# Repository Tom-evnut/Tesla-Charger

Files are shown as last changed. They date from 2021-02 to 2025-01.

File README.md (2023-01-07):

# Tesla-Charger
Reverse Engineering of the Tesla 10Kw charger and development of an open source control board.

PCB Files in DesignSpark 8 format.

Fully built and tested boards and bare PCBs available here :
http://www.evbmw.com/index.php/evbmw-webshop

Support forum : https://openinverter.org/forum/

19/10/17 : Uploaded two files : 
ph_frames.csv this file contains the 3 messages required to run phase module 1 in the Gen 2 charger
power_run_ph1.csv this is a capture of phase 1 starting up , ramping up to 8.5A DC 320VDC, 15.5A AC, 230v 50hz
Mains switched manually around message number 700 in ph_frames.csv

21/10/17 : Uploaded two files : 
power_run_ph1_arduino_2a_365vdc.csv
Tesla_chg1_1.ino
Crude arduino sketch to run one power module in the gen2 charger. Runs on an arduino due on CAN1

01/11/17 : Uploaded design files for Version 1 open source logic board for the Tesla Gen 2 charger. As of this date this design is totally unchecked and untested. Do not build this. It could blow up your house , car or cat. Based on the Arduino Due SAM3X8E microcontroller. Stay tuned.

05/11/17 : Updated Design files and PCBs ordered for prototype builds.

17/11/17 : BOM uploaded for the V1 board.

08/12/17 : Added Tesla_charger_Tom_v2_test.ino source file. Should run all 3 phases with the V1 logic board. Untested.

20/12/17 : Added design files for V2 Charger control board. Major changes :

Added 2M Serial EEPROM for parameter storage

Changed to a Vertical type B USB socket.

23/11/19 : Updated BOM for V4 with corrections.
27/02/18 : Error found on the V2 board. Missing grounds on Q1 and D5. Affects EVSE control only. Will ammend in a rev3 board asap.

28/02/18 : V3 design files released with grounds fixed. Also new S/W thanks to Tom DeBree released but untested as of today. Also pictures of mod required on V1 and V2 boards.

02/05/18 : V3 board and new software tested and working in my BMW E31 project car.

03/01/19 : Added an excellent user manual for the V3 logic board compiled by EVWest.

20/01/19 : Added a Beta Software directory to the Repo. Major changes as of this date :

-Stop sending power module can messages when charger not running - Working.

-Correct reading of charger Fault and Enable feedback signals - Working.

-Correct AC present flag so only sets if more than 70V AC is on each module - Working.

-Reset charger on detection of power module fault - Testing.

-Shutdown on exceeding a preset HV Battery voltage - Working. 

-Evse read routine now in 500ms loop to prevent false triggering -Working.

Recommend using this version.

27/01/19 : Added counter/timer to autoshutdown routine to prevent false triggering on transients.

06/02/19 : On request by a customer:

Added manual control mode for use of charger without EVSE. Digital one in when brought to +12v commands the charger to start
and when brought low commands charger off.

This mode also control HVDC via digital out 1 and AC mains via a contactor via Digital out 2.-Untested as of this date.

19/06/19 : Added schematic for V4 logic board design. V4 has the following upgrades over V3 :

-Changed from Type B USB to Mini. This will allow the charger lid to close without modification.

-Added extra stage of filtering to proximity signal.

-Single wire CAN capability added using the NCV7356. Now uses the exact same switching method between pwm control pilot and sw can as used in the Tesla charger / bms boards. This will allow use of Tesla destination charging, Chademo adapter,CCS adapter and possibly supercharging. All software dependent.

-Added two high power DC low side contactor drivers for use with DC fast charge or as general outputs.

-Added 3rd CAN channel based around the MCP2517 controller. Allows for high speed as well as FD Can. This extra can channel will allow the Tesla charger to act as a Chademo controller. Just add contactors and a hall current sensor.

-Two extra filtered and protected 12v digital inputs. General use or chademo control.

-One extra filtered and protected analog input. General use or hall current sensor for chademo control.

Untested as of this date.

Enjoy!

23/11/19 : Updated BOM for V4 with corrections.

21/01/2020 : New V5 design based on the STM32F103C8T6 now released. Note that as of today no firmware is developed. Anyone want to lend a hand?

18/02/20 : Beata firmware for the V5 board released. Untested as of this release due to hardware delay. Uses ST CUBEIDE.

14.03/20 : ESP8266 based web interface for the V5 charger board using Olimex module. Firmware uploaded. Untested as of release. Bench tests on V5 hardware looking good. One software bug discovered.

12/07/20 : 

Update : V5 software debugging now done.

-EEPROM saving of parameters now working.

-Autoshutdown on exceeding termination voltage parameter now working. 

-WiFi now working

-Correct reporting of voltage and current values over wifi and serial

-Robust reading of pilot pwm current setting. Was very noise prone.

Still todo : 

- Add support for the alternate CAN messaging in some chargers.

Release :

As stated previously due to the lack of engagement / support by the community I employed a developer to debug the firmware at some considerable financial cost and my own time in testing. As such the source for this and further updates will be available to Patrons on Patreon only as of now.
https://www.patreon.com/evbmw

This may change in the future. Binaries are freely available on Github and all boards bought from the EVBMW store will be shipped with this version.
https://github.com/damienmaguire/Tesla-Charger/tree/master/V5/Software/Binary

29/12/20 : Added pdf schematics, board layout and Gerbers for the V5 Block 2 boards (latest release).

24/02/21 : Added pdf schematics, board layout and Gerbers for the V5 Block 3 boards (latest release). Some design improvements to take advantage of the new Openinverter based firmware :

https://openinverter.org/wiki/GEN2

As of this time design files are availabe to Patrons on the "design files" level or greater on Patreon. An opensource release will occur in the future.

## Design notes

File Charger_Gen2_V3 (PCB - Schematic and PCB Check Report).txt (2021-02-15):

Schematic and PCB Check Report
------------------------------

Report Written:     Tuesday, December 18, 2018
Design Path:        C:\Users\tomde\Documents\GitHub\Tesla-Charger\Charger_Gen2_V3.pcb
Design Title:       
Created:            03-Oct-17 12:16:38 PM
Last Saved:         18-Dec-18 12:34:57 PM
Editing Time:       2199 min
Units:              mm (precision 2)

Checking integrity of Schematic "C:\Users\tomde\Documents\GitHub\Tesla-Charger\Charger_Gen2_V3.sch" with PCB "C:\Users\tomde\Documents\GitHub\Tesla-Charger\Charger_Gen2_V3.pcb"
================================================================================================================================================================================

The PCB and Schematic designs do not match.
To bring them into line, you will need to make the following changes to the PCB design:

Component 'C-USC0805' package 'C0805' in PCB is newer version than Schematic, use Update Component to correct this.
Component 'C-USC1206' package 'C1206' in PCB is newer version than Schematic, use Update Component to correct this.
Component 'WE-CBF_0805' package '0805' in PCB is newer version than Schematic, use Update Component to correct this.
Component 'LED0805' package 'CHIPLED_0805' in PCB is newer version than Schematic, use Update Component to correct this.
Component 'R-US_R0805' package 'R0805' in PCB is newer version than Schematic, use Update Component to correct this.
Component 'ATSAM3X/AAU' package 'LQFP144' in PCB is newer version than Schematic, use Update Component to correct this.
Component 'CRYSTAL-3.2-2.5' package 'CRYSTAL-3.2-2.5' in PCB is newer version than Schematic, use Update Component to correct this.
Component 'RESONATOR_EPSON_FC_145' package 'RESONATOR_EPSON_FC_145' in PCB is newer version than Schematic, use Update Component to correct this.
Component 'VARISTORCN0603' package 'CT/CN0603' in PCB is newer version than Schematic, use Update Component to correct this.

End Of Report.

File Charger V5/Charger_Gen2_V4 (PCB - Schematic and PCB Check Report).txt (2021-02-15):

Schematic and PCB Check Report
------------------------------

Report Written:     Monday, January 21, 2019
Design Path:        C:\Users\tomde\Documents\GitHub\Tesla-Charger\Charger V5\Charger_Gen2_V4.pcb
Design Title:       
Created:            03-Oct-17 12:16:38 PM
Last Saved:         21-Jan-19 5:06:33 PM
Editing Time:       2537 min
Units:              mm (precision 2)

Checking integrity of Schematic "C:\Users\tomde\Documents\GitHub\Tesla-Charger\Charger V5\Charger_Gen2_V4.sch" with PCB "C:\Users\tomde\Documents\GitHub\Tesla-Charger\Charger V5\Charger_Gen2_V4.pcb"
======================================================================================================================================================================================================

End Of Report.

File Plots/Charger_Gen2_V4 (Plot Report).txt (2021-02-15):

Plot Report
-----------

Report Written:     Tuesday, December 18, 2018
Design Path:        C:\Users\tomde\Documents\GitHub\Tesla-Charger\Charger_Gen2_V4.pcb
Design Title:       
Created:            03-Oct-17 12:16:38 PM
Last Saved:         18-Dec-18 12:57:42 PM
Editing Time:       2218 min
Units:              mm (precision 2)

Device Settings
===============

Gerber Settings
===============

    Leading zero suppression.
    G01 assumed throughout.
    Line termination <*> <CR> <LF>.
    3.5 format absolute inches.

    Format commands defined in Gerber file.
    Aperture table defined in Gerber file.
    Hardware arcs allowed.

Drill Settings
==============

    Excellon Format 1    Format 3.5 absolute in inches.
    Leading zero suppression.

Plots Output
============

    Plot Job: "C:\Users\tomde\Documents\GitHub\Tesla-Charger\Charger_Gen2_V3.mop"

Gerber Output
=============

C:\Users\tomde\Documents\GitHub\Tesla-Charger\Plots\Charger_Gen2_V4 - Top Copper.gbr

    Layers:
    --------------
    Top Copper

    D-Code Shape  (thou)
    ------------------------------------------------
    D16    Round 10.00
    D19    Round 8.00
    D88    Round 374.02
    D89    Square 76.77
    D90    Round 76.77
    D91    Round 60.00
    D92    Round 59.06
    D93    Round 62.99
    D94    Round 79.72
    D95    Round 43.31
    D96    Round 133.86
    D97    Round 40.00
    D98    Round 19.69
    D99    Round 78.74
    D100   Round 9.84
    D101   Round 39.37
    D102   Round 11.81
    D103   Round 5.91
    D114   Rectangle 29.53 X 129.92  Rotation 90
    D115   Rectangle 151.57 X 196.85  Rotation 90
    D116   Rectangle 55.00 X 60.00
    D117   Rectangle 47.00 X 87.00
    D118   Rectangle 87.00 X 142.00  Rotation 90
    D119   Rectangle 42.13 X 85.04  Rotation 90
    D120   Rectangle 275.59 X 433.07
    D121   Rectangle 153.54 X 212.60
    D122   Rectangle 78.74 X 120.08  Rotation 90
    D123   Rectangle 49.21 X 157.48  Rotation 90
    D124   Rectangle 55.00 X 60.00  Rotation 90
    D125   Rectangle 62.99 X 133.86  Rotation 90
    D126   Square 63.00
    D127   Square 47.24
    D128   Rectangle 51.18 X 59.06
    D129   Rectangle 51.18 X 59.06  Rotation 90
    D130   Rectangle 11.81 X 47.24
    D131   Rectangle 11.81 X 47.24  Rotation 90
    D132   Rectangle 41.34 X 51.18
    D133   Rectangle 43.31 X 70.87
    D134   Square 39.37
    D135   Rectangle 30.00 X 95.00  Rotation 90
    D136   Rectangle 19.69 X 42.32  Rotation 90
    D137   Rectangle 19.69 X 42.32
    D138   Rectangle 27.56 X 39.37  Rotation 90
    D139   Rectangle 21.00 X 67.00  Rotation 90
    D140   Rectangle 27.56 X 60.04  Rotation 90
    D141   Rectangle 25.59 X 60.04  Rotation 90
    D142   Rectangle 25.00 X 50.00
    D143   Rectangle 118.11 X 141.73
    D144   Rectangle 102.36 X 118.11  Rotation 90

Gerber Output
=============

C:\Users\tomde\Documents\GitHub\Tesla-Charger\Plots\Charger_Gen2_V4 - Top Solder Mask.gbr

    Layers:
    -------------------
    Top Solder Mask

    D-Code Shape  (thou)
    ------------------------------------------------
    D118   Round 380.02
    D119   Rectangle 35.53 X 135.92  Rotation 90
    D120   Rectangle 157.57 X 202.85  Rotation 90
    D121   Square 82.77
    D122   Round 82.77
    D123   Rectangle 61.00 X 66.00
    D124   Rectangle 53.00 X 93.00
    D125   Rectangle 93.00 X 148.00  Rotation 90
    D126   Rectangle 48.13 X 91.04  Rotation 90
    D127   Rectangle 281.59 X 439.07
    D128   Rectangle 159.54 X 218.60
    D129   Rectangle 84.74 X 126.08  Rotation 90
    D130   Rectangle 55.21 X 163.48  Rotation 90
    D131   Rectangle 61.00 X 66.00  Rotation 90
    D132   Rectangle 68.99 X 139.86  Rotation 90
    D133   Round 66.00
    D134   Square 69.00
    D135   Square 53.24
    D136   Rectangle 57.18 X 65.06
    D137   Rectangle 57.18 X 65.06  Rotation 90
    D138   Rectangle 17.81 X 53.24
    D139   Rectangle 17.81 X 53.24  Rotation 90
    D140   Rectangle 47.34 X 57.18
    D141   Rectangle 49.31 X 76.87
    D142   Square 45.37
    D143   Rectangle 36.00 X 101.00  Rotation 90
    D144   Rectangle 25.69 X 48.32  Rotation 90
    D145   Rectangle 25.69 X 48.32
    D146   Rectangle 33.56 X 45.37  Rotation 90
    D147   Rectangle 27.00 X 73.00  Rotation 90
    D148   Rectangle 33.56 X 66.04  Rotation 90
    D149   Round 65.06
    D182   Round 68.99
    D183   Rectangle 31.59 X 66.04  Rotation 90
    D184   Round 85.72
    D185   Round 49.31
    D186   Round 139.86
    D187   Rectangle 31.00 X 56.00
    D188   Rectangle 124.11 X 147.73
    D189   Rectangle 108.36 X 124.11  Rotation 90
    D190   Round 46.00
    D191   Round 25.69
    D192   Round 84.74

Gerber Output
=============

C:\Users\tomde\Documents\GitHub\Tesla-Charger\Plots\Charger_Gen2_V4 - Top Paste Mask.gbr

    Layers:
    ------------------
    Top Paste Mask

    D-Code Shape  (thou)
    ------------------------------------------------
    D10    Rectangle 23.53 X 123.92  Rotation 90
    D11    Rectangle 145.57 X 190.85  Rotation 90
    D12    Rectangle 49.00 X 54.00
    D13    Rectangle 41.00 X 81.00
    D14    Rectangle 81.00 X 136.00  Rotation 90
    D15    Rectangle 36.13 X 79.04  Rotation 90
    D16    Rectangle 269.59 X 427.07
    D17    Rectangle 147.54 X 206.60
    D18    Rectangle 72.74 X 114.08  Rotation 90
    D19    Rectangle 43.21 X 151.48  Rotation 90
    D70    Rectangle 49.00 X 54.00  Rotation 90
    D71    Rectangle 56.99 X 127.86  Rotation 90
    D20    Square 57.00
    D21    Square 41.24
    D22    Rectangle 45.18 X 53.06
    D23    Rectangle 45.18 X 53.06  Rotation 90
    D24    Rectangle 5.81 X 41.24
    D25    Rectangle 5.81 X 41.24  Rotation 90
    D26    Rectangle 35.34 X 45.18
    D27    Rectangle 37.31 X 64.87
    D28    Square 33.37
    D29    Rectangle 24.00 X 89.00  Rotation 90
    D72    Rectangle 13.69 X 36.32  Rotation 90
    D73    Rectangle 13.69 X 36.32
    D74    Rectangle 21.56 X 33.37  Rotation 90
    D75    Rectangle 15.00 X 61.00  Rotation 90
    D76    Rectangle 21.56 X 54.04  Rotation 90
    D77    Rectangle 19.59 X 54.04  Rotation 90
    D78    Rectangle 19.00 X 44.00
    D79    Round 1.00
    D80    Rectangle 112.11 X 135.73
    D81    Rectangle 96.36 X 112.11  Rotation 90

Gerber Output
=============

C:\Users\tomde\Documents\GitHub\Tesla-Charger\Plots\Charger_Gen2_V4 - Top Silkscreen.gbr

    Layers:
    ------------------
    Top Silkscreen

    D-Code Shape  (thou)
    -----------------------
    D79    Round 1.00
    D82    Round 5.00
    D83    Round 5.76
    D84    Round 3.20
    D85    Round 4.00
    D86    Round 7.87
    D87    Round 12.00
    D88    Round 10.00
    D89    Round 3.94
    D90    Round 27.56
    D91    Round 8.00
    D92    Round 3.00
    D93    Round 0.80
    D94    Round 6.00
    D95    Round 8.20
    D96    Round 0.00
    D97    Round 25.00
    D98    Round 1.28

Gerber Output
=============

C:\Users\tomde\Documents\GitHub\Tesla-Charger\Plots\Charger_Gen2_V4 - Documentation.gbr

    Layers:
    -----------------
    Documentation

    D-Code Shape  (thou)
    -----------------------
    D82    Round 5.00
    D87    Round 12.00
    D99    Round 1.97

Gerber Output
=============

C:\Users\tomde\Documents\GitHub\Tesla-Charger\Plots\Charger_Gen2_V4 - +5Vcc Plane (Powerplane).gbr

    Layers:
    -------------------------------------------------------------------------------------
    +5Vcc Plane  - Plane Isolation Gap 10.00 Thermal Connect Width 10.00 with 4 Spokes

    D-Code Shape  (thou)
    -----------------------------------------
    D100   Round 394.02
    D101   Square 96.77
    D102   Round 96.77
    D103   Round 80.00
    D104   Round 79.06
    D105   Round 82.99
    D106   Round 99.72
    D107   Round 63.31
    D108   Round 153.86
    D109   Round 40.00  Thermal Relief Pad
    D110   Round 19.69  Thermal Relief Pad
    D111   Round 60.00
    D112   Round 98.74
    D113   Round 39.69

Gerber Output
=============

C:\Users\tomde\Documents\GitHub\Tesla-Charger\Plots\Charger_Gen2_V4 - GND Plane (Powerplane).gbr

    Layers:
    -----------------------------------------------------------------------------------
    GND Plane  - Plane Isolation Gap 10.00 Thermal Connect Width 10.00 with 4 Spokes

    D-Code Shape  (thou)
    -----------------------------------------
    D100   Round 394.02
    D101   Square 96.77
    D102   Round 96.77
    D103   Round 80.00
    D104   Round 79.06
    D105   Round 82.99
    D106   Round 99.72
    D107   Round 76.77  Thermal Relief Pad
    D108   Round 60.00  Thermal Relief Pad
    D109   Round 59.06  Thermal Relief Pad
    D110   Round 62.99  Thermal Relief Pad
    D111   Round 79.72  Thermal Relief Pad
    D112   Round 63.31
    D113   Round 153.86
    D114   Round 60.00
    D115   Round 39.69
    D116   Round 40.00  Thermal Relief Pad
    D117   Round 78.74  Thermal Relief Pad
    D150   Round 19.69  Thermal Relief Pad

Gerber Output
=============

C:\Users\tomde\Documents\GitHub\Tesla-Charger\Plots\Charger_Gen2_V4 - Bottom Copper.gbr

    Layers:
    -----------------
    Bottom Copper

    D-Code Shape  (thou)
    -----------------------
    D10    Round 374.02
    D11    Square 76.77
    D12    Round 76.77
    D13    Round 60.00
    D14    Round 59.06
    D15    Round 62.99
    D16    Round 79.72
    D17    Round 43.31
    D18    Round 133.86
    D19    Round 40.00
    D70    Round 19.69
    D71    Round 78.74
    D20    Round 10.00
    D21    Round 9.84
    D22    Round 39.37
    D23    Round 11.81
    D24    Round 8.00
    D25    Round 5.91

Gerber Output
=============

C:\Users\tomde\Documents\GitHub\Tesla-Charger\Plots\Charger_Gen2_V4 - Bottom Copper (Resist).gbr

    Layers:
    -----------------
    Bottom Copper

    D-Code Shape  (thou)
    -----------------------
    D26    Round 384.02
    D27    Square 86.77
    D28    Round 86.77
    D29    Round 70.00
    D72    Round 69.06
    D73    Round 72.99
    D74    Round 89.72
    D75    Round 53.31
    D76    Round 143.86

Gerber Output
=============

C:\Users\tomde\Documents\GitHub\Tesla-Charger\Plots\Charger_Gen2_V4 - Bottom Copper (Paste).gbr

    Layers:
    -----------------
    Bottom Copper

    D-Code Shape  (thou)
    -----------------------

NC Drill Output
===============

C:\Users\tomde\Documents\GitHub\Tesla-Charger\Plots\Charger_Gen2_V4 - Drill Data - [Through Hole].drl

    Output:
    -----------------------------
    Plated Round Drill Holes
    Unplated Round Drill Holes
    Plated Slots
    Unplated Slots
    Plated Board Outlines
    Unplated Board Outlines

    Tool  Size           Count   ID  (Plated/Unplated)
    -----------------------------------------------------------
    T001  0.01181 inches 131   T
    T002  0.02400 inches 75    I
    T003  0.02500 inches 1
    T004  0.02756 inches 5     R
    T005  0.03200 inches 2     H
    T006  0.03543 inches 7     P
    T007  0.03937 inches 2     C
    T008  0.05118 inches 30    O
    T009  0.05315 inches 4     Q
    T010  0.09055 inches 2     S
    T011  0.17717 inches 6     N
    -----------------------------------------------------------
    Total                265
    -----------------------------------------------------------

Gerber Output
=============

C:\Users\tomde\Documents\GitHub\Tesla-Charger\Plots\Charger_Gen2_V4 - Drill Ident Drawing - [Through Hole].gbr

    Layers:
    ------------------
    [Through Hole]

Drill Ident Drawing
===================

    Drill Plated Size Shape ID
    -----------------------------------
    39    Y      100  Round C
    32    Y      100  Round H
    24    Y      100  Round I
    177   Y      100  Round N
    51    Y      100  Round O
    35    Y      100  Round P
    53    Y      100  Round Q
    28    Y      100  Round R
    91    Y      100  Round S
    12    Y      100  Round T

    D-Code Shape  (thou)
    -----------------------
    D77    Round 100.00
    D78    Round 5.00

Gerber Output
=============

C:\Users\tomde\Documents\GitHub\Tesla-Charger\Plots\Charger_Gen2_V4 - Outline.gbr

    Layers:
    ------------------
    Board Outlines

    D-Code Shape  (thou)
    -----------------------
    D79    Round 12.00

End Of Report.

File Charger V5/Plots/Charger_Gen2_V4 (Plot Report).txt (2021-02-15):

Plot Report
-----------

Report Written:     Thursday, January 24, 2019
Design Path:        C:\Users\tomde\Documents\GitHub\Tesla-Charger\Charger V5\Charger_Gen2_V4.pcb
Design Title:       
Created:            03-Oct-17 12:16:38 PM
Last Saved:         24-Jan-19 4:52:12 PM
Editing Time:       2613 min
Units:              mm (precision 2)

Device Settings
===============

Gerber Settings
===============

    Leading zero suppression.
    G01 assumed throughout.
    Line termination <*> <CR> <LF>.
    3.5 format absolute inches.

    Format commands defined in Gerber file.
    Aperture table defined in Gerber file.
    Hardware arcs allowed.

Drill Settings
==============

    Excellon Format 1    Format 3.5 absolute in inches.
    Leading zero suppression.

Plots Output
============

    Plot Job: "C:\Users\tomde\Documents\GitHub\Tesla-Charger\Charger V5\Charger_Gen2_V4.mop"

Gerber Output
=============

C:\Users\tomde\Documents\GitHub\Tesla-Charger\Charger V5\Plots\Charger_Gen2_V4 - Top Copper.gbr

    Layers:
    --------------
    Top Copper

    D-Code Shape  (thou)
    ------------------------------------------------
    D10    Round 374.02
    D11    Square 76.77
    D12    Round 76.77
    D13    Round 60.00
    D14    Round 59.06
    D15    Round 62.99
    D16    Round 79.72
    D17    Round 43.31
    D18    Round 133.86
    D19    Round 40.00
    D70    Round 19.69
    D71    Round 78.74
    D20    Round 10.00
    D21    Round 9.84
    D22    Round 39.37
    D23    Round 11.81
    D24    Round 8.00
    D25    Round 5.91
    D79    Rectangle 29.53 X 129.92  Rotation 90
    D80    Rectangle 151.57 X 196.85  Rotation 90
    D81    Rectangle 55.00 X 60.00
    D82    Rectangle 47.00 X 87.00
    D83    Rectangle 87.00 X 142.00  Rotation 90
    D84    Rectangle 42.13 X 85.04  Rotation 90
    D85    Rectangle 275.59 X 433.07
    D86    Rectangle 153.54 X 212.60
    D87    Rectangle 78.74 X 120.08  Rotation 90
    D88    Rectangle 49.21 X 157.48  Rotation 90
    D89    Rectangle 55.00 X 60.00  Rotation 90
    D90    Rectangle 62.99 X 133.86  Rotation 90
    D91    Square 63.00
    D92    Square 47.24
    D93    Rectangle 51.18 X 59.06
    D94    Rectangle 51.18 X 59.06  Rotation 90
    D95    Rectangle 11.81 X 47.24
    D96    Rectangle 11.81 X 47.24  Rotation 90
    D97    Rectangle 41.34 X 51.18
    D98    Rectangle 43.31 X 70.87
    D99    Square 39.37
    D100   Rectangle 30.00 X 95.00  Rotation 90
    D101   Rectangle 19.69 X 42.32  Rotation 90
    D102   Rectangle 19.69 X 42.32
    D103   Rectangle 27.56 X 39.37  Rotation 90
    D104   Rectangle 21.00 X 67.00  Rotation 90
    D105   Rectangle 27.56 X 60.04  Rotation 90
    D106   Rectangle 25.59 X 60.04  Rotation 90
    D120   Rectangle 25.00 X 50.00
    D121   Rectangle 118.11 X 141.73
    D122   Rectangle 102.36 X 118.11  Rotation 90

Gerber Output
=============

C:\Users\tomde\Documents\GitHub\Tesla-Charger\Charger V5\Plots\Charger_Gen2_V4 - Top Solder Mask.gbr

    Layers:
    -------------------
    Top Solder Mask

    D-Code Shape  (thou)
    ------------------------------------------------
    D123   Round 380.02
    D124   Rectangle 35.53 X 135.92  Rotation 90
    D125   Rectangle 157.57 X 202.85  Rotation 90
    D126   Square 82.77
    D127   Round 82.77
    D128   Rectangle 61.00 X 66.00
    D129   Rectangle 53.00 X 93.00
    D130   Rectangle 93.00 X 148.00  Rotation 90
    D131   Rectangle 48.13 X 91.04  Rotation 90
    D132   Rectangle 281.59 X 439.07
    D133   Rectangle 159.54 X 218.60
    D134   Rectangle 84.74 X 126.08  Rotation 90
    D135   Rectangle 55.21 X 163.48  Rotation 90
    D136   Rectangle 61.00 X 66.00  Rotation 90
    D137   Rectangle 68.99 X 139.86  Rotation 90
    D138   Round 66.00
    D139   Square 69.00
    D140   Square 53.24
    D141   Rectangle 57.18 X 65.06
    D142   Rectangle 57.18 X 65.06  Rotation 90
    D143   Rectangle 17.81 X 53.24
    D144   Rectangle 17.81 X 53.24  Rotation 90
    D145   Rectangle 47.34 X 57.18
    D146   Rectangle 49.31 X 76.87
    D147   Square 45.37
    D148   Rectangle 36.00 X 101.00  Rotation 90
    D149   Rectangle 25.69 X 48.32  Rotation 90
    D150   Rectangle 25.69 X 48.32
    D151   Rectangle 33.56 X 45.37  Rotation 90
    D152   Rectangle 27.00 X 73.00  Rotation 90
    D153   Rectangle 33.56 X 66.04  Rotation 90
    D154   Round 65.06
    D155   Round 68.99
    D156   Rectangle 31.59 X 66.04  Rotation 90
    D157   Round 85.72
    D158   Round 49.31
    D159   Round 139.86
    D160   Rectangle 31.00 X 56.00
    D161   Rectangle 124.11 X 147.73
    D162   Rectangle 108.36 X 124.11  Rotation 90
    D163   Round 46.00
    D164   Round 25.69
    D165   Round 84.74

Gerber Output
=============

C:\Users\tomde\Documents\GitHub\Tesla-Charger\Charger V5\Plots\Charger_Gen2_V4 - Top Paste Mask.gbr

    Layers:
    ------------------
    Top Paste Mask

    D-Code Shape  (thou)
    ------------------------------------------------
    D150   Rectangle 23.53 X 123.92  Rotation 90
    D151   Rectangle 145.57 X 190.85  Rotation 90
    D152   Rectangle 49.00 X 54.00
    D153   Rectangle 41.00 X 81.00
    D154   Rectangle 81.00 X 136.00  Rotation 90
    D155   Rectangle 36.13 X 79.04  Rotation 90
    D156   Rectangle 269.59 X 427.07
    D157   Rectangle 147.54 X 206.60
    D158   Rectangle 72.74 X 114.08  Rotation 90
    D159   Rectangle 43.21 X 151.48  Rotation 90
    D160   Rectangle 49.00 X 54.00  Rotation 90
    D161   Rectangle 56.99 X 127.86  Rotation 90
    D162   Square 57.00
    D163   Square 41.24
    D164   Rectangle 45.18 X 53.06
    D165   Rectangle 45.18 X 53.06  Rotation 90
    D166   Rectangle 5.81 X 41.24
    D167   Rectangle 5.81 X 41.24  Rotation 90
    D168   Rectangle 35.34 X 45.18
    D169   Rectangle 37.31 X 64.87
    D170   Square 33.37
    D171   Rectangle 24.00 X 89.00  Rotation 90
    D172   Rectangle 13.69 X 36.32  Rotation 90
    D173   Rectangle 13.69 X 36.32
    D174   Rectangle 21.56 X 33.37  Rotation 90
    D175   Rectangle 15.00 X 61.00  Rotation 90
    D176   Rectangle 21.56 X 54.04  Rotation 90
    D177   Rectangle 19.59 X 54.04  Rotation 90
    D178   Rectangle 19.00 X 44.00
    D179   Round 1.00
    D180   Rectangle 112.11 X 135.73
    D181   Rectangle 96.36 X 112.11  Rotation 90

Gerber Output
=============

C:\Users\tomde\Documents\GitHub\Tesla-Charger\Charger V5\Plots\Charger_Gen2_V4 - Top Silkscreen.gbr

    Layers:
    ------------------
    Top Silkscreen

    D-Code Shape  (thou)
    -----------------------
    D10    Round 5.00
    D11    Round 5.76
    D12    Round 3.20
    D13    Round 4.00
    D14    Round 7.87
    D15    Round 12.00
    D16    Round 10.00
    D17    Round 3.94
    D18    Round 27.56
    D19    Round 8.00
    D70    Round 3.00
    D71    Round 0.80
    D20    Round 6.00
    D21    Round 8.20
    D22    Round 0.00
    D23    Round 25.00
    D24    Round 1.28
    D179   Round 1.00

Gerber Output
=============

C:\Users\tomde\Documents\GitHub\Tesla-Charger\Charger V5\Plots\Charger_Gen2_V4 - Documentation.gbr

    Layers:
    -----------------
    Documentation

    D-Code Shape  (thou)
    -----------------------
    D10    Round 5.00
    D15    Round 12.00
    D25    Round 1.97

Gerber Output
=============

C:\Users\tomde\Documents\GitHub\Tesla-Charger\Charger V5\Plots\Charger_Gen2_V4 - +5Vcc Plane (Powerplane).gbr

    Layers:
    -------------------------------------------------------------------------------------
    +5Vcc Plane  - Plane Isolation Gap 10.00 Thermal Connect Width 10.00 with 4 Spokes

    D-Code Shape  (thou)
    -----------------------------------------
    D26    Round 394.02
    D27    Square 96.77
    D28    Round 96.77
    D29    Round 80.00
    D72    Round 79.06
    D73    Round 82.99
    D74    Round 99.72
    D75    Round 43.31  Thermal Relief Pad
    D76    Round 63.31
    D77    Round 153.86
    D78    Round 40.00  Thermal Relief Pad
    D79    Round 19.69  Thermal Relief Pad
    D80    Round 60.00
    D81    Round 98.74
    D82    Round 39.69

Gerber Output
=============

C:\Users\tomde\Documents\GitHub\Tesla-Charger\Charger V5\Plots\Charger_Gen2_V4 - GND Plane (Powerplane).gbr

    Layers:
    -----------------------------------------------------------------------------------
    GND Plane  - Plane Isolation Gap 10.00 Thermal Connect Width 10.00 with 4 Spokes

    D-Code Shape  (thou)
    -----------------------------------------
    D26    Round 394.02
    D27    Square 96.77
    D28    Round 96.77
    D29    Round 80.00
    D72    Round 79.06
    D73    Round 82.99
    D74    Round 99.72
    D75    Round 43.31  Thermal Relief Pad
    D76    Round 63.31
    D77    Round 153.86
    D78    Round 40.00  Thermal Relief Pad
    D79    Round 19.69  Thermal Relief Pad
    D80    Round 60.00
    D82    Round 39.69
    D83    Round 76.77  Thermal Relief Pad
    D84    Round 60.00  Thermal Relief Pad
    D85    Round 59.06  Thermal Relief Pad
    D86    Round 62.99  Thermal Relief Pad
    D87    Round 79.72  Thermal Relief Pad
    D88    Round 78.74  Thermal Relief Pad

Gerber Output
=============

C:\Users\tomde\Documents\GitHub\Tesla-Charger\Charger V5\Plots\Charger_Gen2_V4 - Bottom Copper.gbr

    Layers:
    -----------------
    Bottom Copper

    D-Code Shape  (thou)
    -----------------------
    D16    Round 10.00
    D19    Round 8.00
    D89    Round 374.02
    D90    Square 76.77
    D91    Round 76.77
    D92    Round 60.00
    D93    Round 59.06
    D94    Round 62.99
    D95    Round 79.72
    D96    Round 43.31
    D97    Round 133.86
    D98    Round 40.00
    D99    Round 19.69
    D100   Round 78.74
    D101   Round 9.84
    D102   Round 39.37
    D103   Round 11.81
    D104   Round 5.91

Gerber Output
=============

C:\Users\tomde\Documents\GitHub\Tesla-Charger\Charger V5\Plots\Charger_Gen2_V4 - Bottom Copper (Resist).gbr

    Layers:
    -----------------
    Bottom Copper

    D-Code Shape  (thou)
    -----------------------
    D105   Round 384.02
    D106   Square 86.77
    D107   Round 86.77
    D108   Round 70.00
    D109   Round 69.06
    D110   Round 72.99
    D111   Round 89.72
    D112   Round 53.31
    D113   Round 143.86

Gerber Output
=============

C:\Users\tomde\Documents\GitHub\Tesla-Charger\Charger V5\Plots\Charger_Gen2_V4 - Bottom Copper (Paste).gbr

    Layers:
    -----------------
    Bottom Copper

    D-Code Shape  (thou)
    -----------------------

NC Drill Output
===============

C:\Users\tomde\Documents\GitHub\Tesla-Charger\Charger V5\Plots\Charger_Gen2_V4 - Drill Data - [Through Hole].drl

    Output:
    -----------------------------
    Plated Round Drill Holes
    Unplated Round Drill Holes
    Plated Slots
    Unplated Slots
    Plated Board Outlines
    Unplated Board Outlines

    Tool  Size           Count   ID  (Plated/Unplated)
    -----------------------------------------------------------
    T001  0.01181 inches 131   T
    T002  0.02400 inches 75    I
    T003  0.02500 inches 1
    T004  0.02756 inches 5     R
    T005  0.03200 inches 2     H
    T006  0.03543 inches 7     P
    T007  0.03937 inches 2     C
    T008  0.05118 inches 30    O
    T009  0.05315 inches 4     Q
    T010  0.09055 inches 2     S
    T011  0.17717 inches 6     N
    -----------------------------------------------------------
    Total                265
    -----------------------------------------------------------

Gerber Output
=============

C:\Users\tomde\Documents\GitHub\Tesla-Charger\Charger V5\Plots\Charger_Gen2_V4 - Drill Ident Drawing - [Through Hole].gbr

    Layers:
    ------------------
    [Through Hole]

Drill Ident Drawing
===================

    Drill Plated Size Shape ID
    -----------------------------------
    39    Y      100  Round C
    32    Y      100  Round H
    24    Y      100  Round I
    177   Y      100  Round N
    51    Y      100  Round O
    35    Y      100  Round P
    53    Y      100  Round Q
    28    Y      100  Round R
    91    Y      100  Round S
    12    Y      100  Round T

    D-Code Shape  (thou)
    -----------------------
    D10    Round 5.00
    D114   Round 100.00

End Of Report.

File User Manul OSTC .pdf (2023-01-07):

## Serial Control Open Source Tesla Charger

By Tom de Bree 12/11/2018

## Contents

### Command Index

‘s’ to toggle the charge on and off by serial command, will be overridden in auto start and can control

‘d’ stops the debug and displays all the values currently set, will bring up display like below

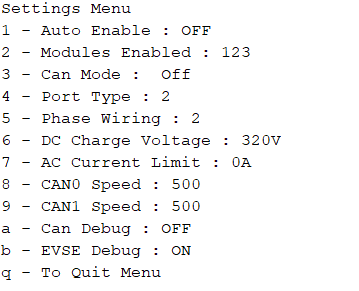
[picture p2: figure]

‘1’ to toggle auto enable, this looks at the pilot and proximity signal to turn the charger on and off.

‘2’ followed by which charger modules to enable; ‘12’ would enable module 1 and 2

‘3’ followed by a

‘0’ to disable can mode

‘1’ to enable can mode : Master

‘2’ to enable can mode : Master Elcon

‘3’ to enable can mode : Slave

‘4’ followed by a ‘1’ for a type 1 socket and ‘2’ for a type 2 socket.

‘5’ followed by a ‘1’ for single phase setup and ‘3’ for a three phase setup

‘6’ followed by the value for desired DC voltage in whole numbers in V

‘7’ followed by the value for desired AC current in whole numbers in A

‘8’ followed by a number to set canbus 1 speeds; ex: ‘8 250’ will give you a speed of 250 000 baud

‘9’ followed by a number to set canbus 1 speeds; ex: ‘9 250’ will give you a speed of 250 000 baud

‘a’ to toggle the Can Debug to be enabled once exiting the settings menu

‘b’ to toggle the EVSE Debug to be enabled once exiting the settings menu

## Recommended test settings

### Setup for using with EVSE

This setup is meant to be used when a charger is connected to a charging port and is meant to be used with an EVSE

- set it to can mode Master
- set it to autostart mode
- set 5 amp ac input limit per phase
- set end voltage limit suited to pack
- set to type 2 socket or set it to ‘t1’ for the type 1 socket
- Phase ‘3’ – if all modules are on their own phase, else use ‘1’

To initiate charge connect HV to charger and insert EVSE plug into socket.

If all works as expected change the input limit to match the wiring and breaker limits.

### Setup for using without EVSE

This setup is meant to be used when a charger is connected to a charging port and will not be used with an EVSE.

- set it to can master mode
- set it to No autostart mode
- set a 5 amp ac input limit per phase
- set end voltage limit suited to pack
- Phase ‘3’ – if all modules are on their own phase, else use ‘1’

To initiate charge connect HV to charger, command ‘s’ and apply AC power once module readouts appear on serial console.

If all works as expected change the input limit to match the wiring and breaker limits.

### Setup for configuring a Slave Charger

This setup is meant to be used when a charger is the second charger in a set. The other charger needs to be set to Can Mode: Master or Master Elcon.

- set it to can mode Slave
- set it to no autostart mode
- set a 5 amp ac input limit per phase
- set end voltage limit suited to pack
- Phase ‘3’ – if all modules are on their own phase, else use ‘1’

To initiate charge connect HV to charger and get the master charger to start charging (AC current limit for master charger needs to be above 15A). The slave charger will initiate shortly after the master.

If all works as expected change the input limit to match the wiring and breaker limits.

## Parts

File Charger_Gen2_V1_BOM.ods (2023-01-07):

Tesla Gen 2 Charger Logic Board V1
Ref Name | Qty | Component | Value | Manufacturer | MPN | RS Part Number | Mouser Part Number | Description
D3,4,5 | 3 | 1N4148WS-7-F |  | Diodes Inc. | 1N4148WS-7-F | 9228070 |  | Diode Switching 150mA 75V 200mW SOD323 Diodes Inc 1N4148WS-7-F Switching Diode, 150mA 75V, 2-Pin SOD-323
CONN3,4 | 2 | 3WAY_SIL |  | AMPHENOL FCI | 77311-401-36LF | 771-0189 |  | Board-To-Board Connector, 2.54 mm, 36 Contacts, Header, BergStik 77311 Series, Through Hole, 1 Rows
CONN2 | 1 | IPS1-115-01-S-D-PL |  | SAMTEC | IPS1-115-01-S-D-PL | 767-6859 |  | SAMTEC - IPS1-115-01-S-D-PL - SOCKET, 2.54MM, 2X15WAY
CONN1 | 1 | 24PinJSTCPT |  | JST (JAPAN SOLDERLESS TERMINALS) | SM24B-CPTK-1A-TB(L) |  | 306-SM24B-CPTK-1ATBL | Automotive Connectors 24 POS SIDE ENTRY CPT MALE CONN
L1 | 1 | 7447709470 |  | Wurth Elektronik | 7447709470 | 789-6805 |  | Surface Mount Power Inductor, WE-PD Series, 47 µH, 3.8 A, 4.5 A, Shielded, 0.06 ohm
IC1 | 1 | ATSAM3X/AAU | ATSAM3X8EA-AU | Microchip | ATSAM3X8EA-AU | 131-1191 | 556-ATSAM3X8EA-AU | ATSAM3X8EA-AU, 32bit ARM Cortex M3 Microcontroller, 84MHz, 512 kB Flash, 144-Pin LQFP
C2,4,5,6,7,8,9,11,14,15,16,18,19,20,21,22,23,36,106,107,109,110 | 22 | C-USC0805 | 0.1u | MURATA | GRM219R71C104KA01D | 790-0667 |  | 100nF Multilayer Ceramic Capacitor MLCC 16V dc ±10% X7R Dielectric 0805 (2012M)
C30 | 1 | C-USC0805 | 0.01u | AVX | 08055F103KAT2A | 698-3462 |  | 10nF Multilayer Ceramic Capacitor MLCC 50V dc ±10% X8R Dielectric 0805 (2012M)
C111,112,37 | 3 | C-USC0805 | 1uF | KEMET | C0805C105K4RACTU | 451-5770 |  | 1μF Multilayer Ceramic Capacitor MLCC 16V dc ±10% X7R Dielectric 0805 (2012M)
C1,10,12,13,24,31,17 | 7 | C-USC0805 | 10u | MURATA | GRM21BR61E106KA73L | 790-0673 |  | 10μF Multilayer Ceramic Capacitor MLCC 25V dc ±10% X5R Dielectric 0805 (2012M)
C27,28,29 | 3 | C-USC0805 | 22p | AVX | 08051A220JAT2A | 464-6587 |  | 22pF Multilayer Ceramic Capacitor MLCC 100V dc ±5% C0G Dielectric 0805 (2012M)
C105,108 | 2 | C-USC0805 | 47nF | AVX | 08055F473KAT2A |  |  | 47nF Multilayer Ceramic Capacitor MLCC 50V dc ±10% X8R Dielectric 0805 (2012M)
C25,26 | 2 | C-USC1206 | 22p | AVX | 12061A220JAT2A | 136-4302 |  | AVX 22pF Multilayer Ceramic Capacitor (MLCC) 100V dc ±5% 1206 (3216M)
C3 | 1 | Cap_el | 100uF | RSPRO | 711-0703 | 711-0703 |  | Aluminium Electrolytic Capacitor 100μF 6.3V dc 5mm Through Hole
Y1 | 1 | CRYSTAL-3.2-2.5 | 12MHz KX-7 20pF | ECS | ECS-120-20-33-CKM-TR |  | 520-120-20-33-CKMT | Crystals 12.000MHz 20pF 10ppm -20C +70C
C38 | 1 | EEEFK1A221XP | 220uF | Panasonic | EEEFK1A221XP | 7083342 |  | Ecap 220uF 10V D8 Case FK SMD Panasonic 220F 10 V dc Aluminium Electrolytic Capacitor, FK SMD Series 2000h 6.3 Dia. x 7.7mm
C35 | 1 | EEVEB2C680SM | 680uF | Panasonic | EEVEB2C680SM |  |  | PANASONIC ELECTRONIC COMPONENTS - EEVEB2C680SM - CAP, ALU ELEC, 68UF, 160V, SMD
LD1 | 1 | LD1117SOT223 | LD1117-3.3 | STMICROELECTRONICS | LD1117S33CTR | 686-9388 |  | LD1117S33CTR, LDO Regulator, 1.3A, 3.3 V, ±1% 3+Tab-Pin, SOT-223
LED1,2 | 1 | LED0805 |  | Wurth Elektronik | 150080SS75000 |  |  | Wurth Elektronik 150080SS75000, WL-SMCW 630 nm Red LED, 2012 (0805) Clear SMD package
IC6 | 1 | LM2596S-5.0_NOPB |  | Texas Instruments | LM2596S-5.0/NOPB | 5333692 |  | SIMPLE SWITCHER 4.5V to 40V, 3A Low Component Count Step-Down Regulator
D1,2 | 1 | MBRS540T3G |  | ON Semiconductor | MBRS540T3G | 1250012 |  | Diode Schottky 40V 5A SMC ON Semiconductor MBRS540T3G Schottky Diode, 5A, 40V, 2-Pin SMC
Q1 | 1 | MMBT3904 |  | Fairchild Semiconductor | MMBT3904 | 7390303 |  | Transistor GP BJT NPN 40V 0.2A SOT23 Fairchild MMBT3904 NPN Bipolar Transistor, 0.2 A, 40 V, 3-Pin SOT-23
X1 | 1 | PN61729-S | PN61729-S | AMPHENOL FCI | 61729-0010BLF | 771-0035 |  | Amphenol FCI 1 Port Right Angle Through Hole Mount Female Version 2.0 Type B USB Connector
ERASE | 1 | PUSHBUTTON | PUSHBUTTON | TE Connectivity | 147873-1 | 131-4769 |  | Black Slide Tactile Switch, SPST 50 mA 1.5mm Surface Mount
RESET | 1 | PUSHBUTTON | PUSHBUTTON | TE Connectivity | 147873-1 | 131-4769 |  | Black Slide Tactile Switch, SPST 50 mA 1.5mm Surface Mount
R12 | 1 | R-US_R0805 | 0R | RSPRO | RS-0805-0R-5%-0.125W | 717-1578 |  | Thick Film Surface Mount Fixed Resistor 0805 Case 0Ω ±5% 0.125W
R9 | 1 | R-US_R0805 | 1K | RSPRO | 804-6449 | 804-6449 |  | Thick Film Surface Mount Fixed Resistor 0805 Case 1kΩ ±1% 0.125W
R7 | 1 | R-US_R0805 | 1K3 | RSPRO | RS-0805-1k3-5%-0.125W | 713-6945 |  | RS Series Thick Film Surface Mount Resistor 0805 Case 1.3kΩ ±5% 0.125W
R15,17 | 2 | R-US_R0805 | 1K5 | RSPRO | RS-0805-1k5-5%-0.125W | 713-6954 |  | Thick Film Surface Mount Fixed Resistor 0805 Case 1.5kΩ ±5% 0.125W
R6 | 1 | R-US_R0805 | 2K7 | RSPRO | 804-6486 | 804-6486 |  | Thick Film Surface Mount Fixed Resistor 0805 Case 2.7kΩ ±1% 0.125W
R14,16 | 2 | R-US_R0805 | 4K7 | RSPRO | RS-0805-4k7-5%-0.125W | 713-6998 |  | Thick Film Surface Mount Fixed Resistor 0805 Case 4.7kΩ ±5% 0.125W
R4 | 1 | R-US_R0805 | 6k8 1% | RSPRO | 804-6515 | 804-6515 |  | Thick Film Surface Mount Fixed Resistor 0805 Case 6.8kΩ ±1% 0.125W
R8 | 1 | R-US_R0805 | 22K | RSPRO | 804-6546 | 804-6546 |  | Thick Film Surface Mount Fixed Resistor 0805 Case 22kΩ ±1% 0.125W
R2,3 | 2 | R-US_R0805 | 39R | RSPRO | 804-6335 | 804-6335 |  | Thick Film Surface Mount Fixed Resistor 0805 Case 39Ω ±1% 0.125W
R69,70,71,72 | 4 | R-US_R0805 | 60R4 | RSPRO | RS-0805-60R4-1%-0.125W | 717-2130 |  | Thick Film Surface Mount Fixed Resistor 0805 Case 60.4Ω ±1% 0.125W
R1 | 1 | R-US_R0805 | 100k | RSPRO | 804-6607 | 804-6607 |  | Thick Film Surface Mount Fixed Resistor 0805 Case 100kΩ ±1% 0.125W
R10 | 1 | R-US_R0805 | 330R | RSPRO | 804-6401 | 804-6401 |  | Thick Film Surface Mount Fixed Resistor 0805 Case 330Ω ±1% 0.125W
R5,13 | 2 | R-US_R0805 | 390R | RSPRO | RS-0805-390R-5%-0.125W | 713-6907 |  | Thick Film Surface Mount Fixed Resistor 0805 Case 390Ω ±5% 0.125W
R11 | 1 | R-US_R0805 | 680R | RSPRO | 804-6423 | 804-6423 |  | Thick Film Surface Mount Fixed Resistor 0805 Case 680Ω ±1% 0.125W
Y2 | 1 | RESONATOR_EPSON_FC_145 | 32.768Khz | EPSON TOYOCOM | FC-135 32.768KHz 20ppm, 7pF | 667-6094 |  | SMD Crystal 32.768kHz, ±20ppm, 2-Pin, 3.2 x 1.5 x 0.8mm
IC3,4 | 2 | SN65HVD234 | SN65HVD234 | Texas Instruments | SN65HVD234D | 662-4315 |  | SN65HVD234D, CAN Transceiver 1MBps 1-channel ISO 11898
IC2 | 1 | SN74AHCT125D |  | Texas Instruments | SN74AHCT125D | 526606 |  | SN74AHCT125D, Quad Bus Buffer, 7.5 ns @ 5 V 8mA, 4.5 → 5.5 V, 14-Pin SOIC
IC5 | 1 | ULN2003ADR |  | Texas Instruments | ULN2003ADR | 6658699P |  | Trans Darlington NPN 50V 0.5A SOIC16 Texas Instruments ULN2003ADR, 7-element NPN Darlington Transistor Array, 0.5 A 50 V, 16-Pin SOIC
Z1,2 | 1 | VARISTORCN0603 | CG0603MLC-05E | Bourns | CG0603MLC-05E | 851-8256 |  | MLC Series Power Varistor 0.5pF, Clamping 20V 0603 (1608M)
L2,3,4,5 | 4 | WE-CBF_0805 | MH2029-300Y |  |  |  |  | SMD EMI Suppression Ferrite Beads- excellent anti-EMI properties - low DCR- impedances till 3000 ohms- rated current up to 6 A

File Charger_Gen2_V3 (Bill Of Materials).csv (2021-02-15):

Report Written: | Tuesday, December 18, 2018
Design Path: | C:\Users\tomde\Documents\GitHub\Tesla-Charger\Charger_Gen2_V3.pcb
Design Title:
Created: | 03-10-17 12:16
Last Saved: | 18-12-18 12:48
Editing Time: | 2214 min
Units: | mm (precision 2)
Bill of Materials generated with DesignSpark PCB - www.DesignSpark.com/pcb
--------------------------------------------------------------------------
Ref Name | Qty | Component | Value | Package | Manufacturer | MPN | RS Part Number | Other Part Number | Description
D3 | 1 | 1N4148WS-7-F |  | SOD2513X120N | Diodes Inc. | 1N4148WS-7-F | 9228070 |  | Diode Switching 150mA 75V 200mW SOD323 Diodes Inc 1N4148WS-7-F Switching Diode, 150mA 75V, 2-Pin SOD-323
D4 | 1 | 1N4148WS-7-F |  | SOD2513X120N | Diodes Inc. | 1N4148WS-7-F | 9228070 |  | Diode Switching 150mA 75V 200mW SOD323 Diodes Inc 1N4148WS-7-F Switching Diode, 150mA 75V, 2-Pin SOD-323
D5 | 1 | 1N4148WS-7-F |  | SOD2513X120N | Diodes Inc. | 1N4148WS-7-F | 9228070 |  | Diode Switching 150mA 75V 200mW SOD323 Diodes Inc 1N4148WS-7-F Switching Diode, 150mA 75V, 2-Pin SOD-323
CONN3 | 1 | 3WAY_SIL |  | DIL
CONN4 | 1 | 4waysil |  | DSC
CONN1 | 1 | 24PinJSTCPT |  | DSC
L1 | 1 | 7447709470 |  | WE-PD_1260/1245/1280/121054 | Würth Elektronik | 7447709470 |  |  | SMD-Shielded Power Inductors WE-PD
J1 | 1 | 5000751517 |  | 5000751517 | Molex | 5000751517 |  |  | USB On-The-Go (OTG) Mini-B Receptacle, Vertical, Through Hole Solder Tails and Shell Tabs
IC1 | 1 | ATSAM3X/AAU | ATSAM3X8EA-AU | LQFP144
C2 | 1 | C-USC0805 | 0.1u | C0805 |  |  |  |  | CAPACITOR, American symbol
C4 | 1 | C-USC0805 | 0.1u | C0805 |  |  |  |  | CAPACITOR, American symbol
C5 | 1 | C-USC0805 | 0.1u | C0805 |  |  |  |  | CAPACITOR, American symbol
C6 | 1 | C-USC0805 | 0.1u | C0805 |  |  |  |  | CAPACITOR, American symbol
C7 | 1 | C-USC0805 | 0.1u | C0805 |  |  |  |  | CAPACITOR, American symbol
C8 | 1 | C-USC0805 | 0.1u | C0805 |  |  |  |  | CAPACITOR, American symbol
C9 | 1 | C-USC0805 | 0.1u | C0805 |  |  |  |  | CAPACITOR, American symbol
C11 | 1 | C-USC0805 | 0.1u | C0805 |  |  |  |  | CAPACITOR, American symbol
C14 | 1 | C-USC0805 | 0.1u | C0805 |  |  |  |  | CAPACITOR, American symbol
C15 | 1 | C-USC0805 | 0.1u | C0805 |  |  |  |  | CAPACITOR, American symbol
C16 | 1 | C-USC0805 | 0.1u | C0805 |  |  |  |  | CAPACITOR, American symbol
C18 | 1 | C-USC0805 | 0.1u | C0805 |  |  |  |  | CAPACITOR, American symbol
C19 | 1 | C-USC0805 | 0.1u | C0805 |  |  |  |  | CAPACITOR, American symbol
C20 | 1 | C-USC0805 | 0.1u | C0805 |  |  |  |  | CAPACITOR, American symbol
C21 | 1 | C-USC0805 | 0.1u | C0805 |  |  |  |  | CAPACITOR, American symbol
C22 | 1 | C-USC0805 | 0.1u | C0805 |  |  |  |  | CAPACITOR, American symbol
C23 | 1 | C-USC0805 | 0.1u | C0805 |  |  |  |  | CAPACITOR, American symbol
C32 | 1 | C-USC0805 | 0.1u | C0805 |  |  |  |  | CAPACITOR, American symbol
C106 | 1 | C-USC0805 | 0.1uF | C0805 |  |  |  |  | CAPACITOR, American symbol
C107 | 1 | C-USC0805 | 0.1uF | C0805 |  |  |  |  | CAPACITOR, American symbol
C109 | 1 | C-USC0805 | 0.1uF | C0805 |  |  |  |  | CAPACITOR, American symbol
C110 | 1 | C-USC0805 | 0.1uF | C0805 |  |  |  |  | CAPACITOR, American symbol
C30 | 1 | C-USC0805 | 0.01u | C0805 |  |  |  |  | CAPACITOR, American symbol
C111 | 1 | C-USC0805 | 1uF | C0805 |  |  |  |  | CAPACITOR, American symbol
C112 | 1 | C-USC0805 | 1uF | C0805 |  |  |  |  | CAPACITOR, American symbol
C1 | 1 | C-USC0805 | 10u | C0805 |  |  |  |  | CAPACITOR, American symbol
C10 | 1 | C-USC0805 | 10u | C0805 |  |  |  |  | CAPACITOR, American symbol
C12 | 1 | C-USC0805 | 10u | C0805 |  |  |  |  | CAPACITOR, American symbol
C13 | 1 | C-USC0805 | 10u | C0805 |  |  |  |  | CAPACITOR, American symbol
C24 | 1 | C-USC0805 | 10u | C0805 |  |  |  |  | CAPACITOR, American symbol
C31 | 1 | C-USC0805 | 10u | C0805 |  |  |  |  | CAPACITOR, American symbol
C27 | 1 | C-USC0805 | 22p | C0805 |  |  |  |  | CAPACITOR, American symbol
C28 | 1 | C-USC0805 | 22p | C0805 |  |  |  |  | CAPACITOR, American symbol
C29 | 1 | C-USC0805 | 22p | C0805 |  |  |  |  | CAPACITOR, American symbol
C105 | 1 | C-USC0805 | 47nF | C0805 |  |  |  |  | CAPACITOR, American symbol
C108 | 1 | C-USC0805 | 47nF | C0805 |  |  |  |  | CAPACITOR, American symbol
C25 | 1 | C-USC1206 | 22p | C1206 |  |  |  |  | CAPACITOR, American symbol
C26 | 1 | C-USC1206 | 22p | C1206 |  |  |  |  | CAPACITOR, American symbol
C3 | 1 | Cap_el | 100uF | DSC
Y1 | 1 | CRYSTAL-3.2-2.5 | 12MHz KX-7 20pF | CRYSTAL-3.2-2.5
C36 | 1 | C_0805 | 0.1uF | C0805 |  |  |  |  | NON-POLARIZED CAP
C37 | 1 | C_0805 | 1uF | C0805 |  |  |  |  | NON-POLARIZED CAP
C17 | 1 | C_0805 | 10uF | C0805 |  |  |  |  | NON-POLARIZED CAP
C38 | 1 | EEEFK1A221XP | 220uF | FKSV(D8) | Panasonic | EEEFK1A221XP | 7083342 |  | Ecap 220uF 10V D8 Case FK SMD Panasonic 220F 10 V dc Aluminium Electrolytic Capacitor, FK SMD Series 2000h 6.3 Dia. x 7.7mm
C35 | 1 | EEVEB2C680SM | 680uF | EBV(K16) | Panasonic | EEVEB2C680SM |  |  | PANASONIC ELECTRONIC COMPONENTS - EEVEB2C680SM - CAP, ALU ELEC, 68UF, 160V, SMD
S1 | 1 | EVQPE505K |  | EVQPE505K | Panasonic | EVQPE505K | 7561565 |  | Tact switch,THT,SPST,black,1.6N op force Black Push Plate Tactile Switch, SPST-NO 50 mA 5mm
S2 | 1 | EVQPE505K |  | EVQPE505K | Panasonic | EVQPE505K | 7561565 |  | Tact switch,THT,SPST,black,1.6N op force Black Push Plate Tactile Switch, SPST-NO 50 mA 5mm
CONN2 | 1 | IPS1-115-01-S-D-PL |  | SHDR30W109P254_2X15_3810X495X8 | SAMTEC | IPS1-115-01-S-D-PL |  |  | SAMTEC - IPS1-115-01-S-D-PL - SOCKET, 2.54MM, 2X15WAY
LD1 | 1 | LD1117SOT223 | LD1117-3.3 | SOT223
LED1 | 1 | LED0805 |  | CHIPLED_0805 |  |  |  |  | LED0603 - 0603 Surface Mount Package2mA:Green LED - Low Power (3.9mcd, 2ma, 1.7Vf) - Digikey: 475-2709-2-NDOrange LED - Low Power (9.8mcd, 2ma, 1.8Vf) - Digikey: 475-1194-2-NDRed LED - Low Power (5mcd, 2ma, 1.8Vf) - Digikey: 475-1195-2-NDYellow LED - Low Power (7mcd, 2ma, 1.8Vf) - Digikey: 475-1196-2-ND5mA:Blue LED - Low Power (17mcd, 5ma, 2.9Vf) - Digikey: LNJ937W8CRACT-ND0805 - 0805 Surface Mount Package2mA:Red LED (8.8mcd, 2mA, 1.8Vf, Clear) - Low Power [Digikey: 475-2510-1-ND]Green LED (5mcd, 2mA, 1.8Vf, Clear) - Low Power [Digikey: 475-2730-1-ND]Yellow LED (11.3mcd, 2mA, 1.8Vf, Clear) - Low Power [Digikey: 475-2555-1-ND]20mA:Red LED (104mcd, 20mA, Diffused) - LS R976 [Digikey: 475-1278-6-ND]Red LED (12mcd, 20mA, 2.0Vf, Clear) - APT2012EC [Digikey: 754-1128-1-ND]Green LED (15mcd, 20mA, 2.2Vf, Clear) - APT2012GC [Digikey: 754-1131-1-ND]Orange LED (160mcd, 20mA, 2.1Vf, Clear) - APT2012SECK [Digikey: 754-1130-1-ND]1206 - 1206 Surface Mount PackageGreen LED (26mcd, 20mA, Diffused) - LG N971 [Digikey: 475-1407-6-ND]Red LED (15mcd, 20mA, Diffused) - LH N974 [Digikey: 475-1416-6-ND]
LED2 | 1 | LED0805 |  | CHIPLED_0805 |  |  |  |  | LED0603 - 0603 Surface Mount Package2mA:Green LED - Low Power (3.9mcd, 2ma, 1.7Vf) - Digikey: 475-2709-2-NDOrange LED - Low Power (9.8mcd, 2ma, 1.8Vf) - Digikey: 475-1194-2-NDRed LED - Low Power (5mcd, 2ma, 1.8Vf) - Digikey: 475-1195-2-NDYellow LED - Low Power (7mcd, 2ma, 1.8Vf) - Digikey: 475-1196-2-ND5mA:Blue LED - Low Power (17mcd, 5ma, 2.9Vf) - Digikey: LNJ937W8CRACT-ND0805 - 0805 Surface Mount Package2mA:Red LED (8.8mcd, 2mA, 1.8Vf, Clear) - Low Power [Digikey: 475-2510-1-ND]Green LED (5mcd, 2mA, 1.8Vf, Clear) - Low Power [Digikey: 475-2730-1-ND]Yellow LED (11.3mcd, 2mA, 1.8Vf, Clear) - Low Power [Digikey: 475-2555-1-ND]20mA:Red LED (104mcd, 20mA, Diffused) - LS R976 [Digikey: 475-1278-6-ND]Red LED (12mcd, 20mA, 2.0Vf, Clear) - APT2012EC [Digikey: 754-1128-1-ND]Green LED (15mcd, 20mA, 2.2Vf, Clear) - APT2012GC [Digikey: 754-1131-1-ND]Orange LED (160mcd, 20mA, 2.1Vf, Clear) - APT2012SECK [Digikey: 754-1130-1-ND]1206 - 1206 Surface Mount PackageGreen LED (26mcd, 20mA, Diffused) - LG N971 [Digikey: 475-1407-6-ND]Red LED (15mcd, 20mA, Diffused) - LH N974 [Digikey: 475-1416-6-ND]
IC6 | 1 | LM2596S-5.0_NOPB |  | TO170P1435X465-6N | Texas Instruments | LM2596S-5.0/NOPB | 5333692 |  | SIMPLE SWITCHER 4.5V to 40V, 3A Low Component Count Step-Down Regulator
IC7 | 1 | M24M02-DRMN6TP |  | SOIC127P600X175-8N | STMicroelectronics | M24M02-DRMN6TP | 8805333 |  | STMicroelectronics M24M02-DRMN6TP EEPROM Memory, 2Mbit, 450ns, 1.8 5.5 V 8-Pin SOIC
D1 | 1 | MBRS540T3G |  | DIOM7958X256N | ON Semiconductor | MBRS540T3G | 1250012 |  | Diode Schottky 40V 5A SMC ON Semiconductor MBRS540T3G Schottky Diode, 5A, 40V, 2-Pin SMC
D2 | 1 | MBRS540T3G |  | DIOM7958X256N | ON Semiconductor | MBRS540T3G | 1250012 |  | Diode Schottky 40V 5A SMC ON Semiconductor MBRS540T3G Schottky Diode, 5A, 40V, 2-Pin SMC
Q1 | 1 | MMBT3904 |  | SOT95P240X93-3N | Fairchild Semiconductor | MMBT3904 | 7390303 |  | Transistor GP BJT NPN 40V 0.2A SOT23 Fairchild MMBT3904 NPN Bipolar Transistor, 0.2 A, 40 V, 3-Pin SOT-23
R12 | 1 | R-US_R0805 | 0R | R0805 |  |  |  |  | RESISTOR, American symbol
R9 | 1 | R-US_R0805 | 1K | R0805 |  |  |  |  | RESISTOR, American symbol
R7 | 1 | R-US_R0805 | 1K3 | R0805 |  |  |  |  | RESISTOR, American symbol
R15 | 1 | R-US_R0805 | 1K5 | R0805 |  |  |  |  | RESISTOR, American symbol
R17 | 1 | R-US_R0805 | 1K5 | R0805 |  |  |  |  | RESISTOR, American symbol
R6 | 1 | R-US_R0805 | 2K7 | R0805 |  |  |  |  | RESISTOR, American symbol
R14 | 1 | R-US_R0805 | 4K7 | R0805 |  |  |  |  | RESISTOR, American symbol
R16 | 1 | R-US_R0805 | 4K7 | R0805 |  |  |  |  | RESISTOR, American symbol
R18 | 1 | R-US_R0805 | 4K7 | R0805 |  |  |  |  | RESISTOR, American symbol
R19 | 1 | R-US_R0805 | 4K7 | R0805 |  |  |  |  | RESISTOR, American symbol
R4 | 1 | R-US_R0805 | 6k8 1% | R0805 |  |  |  |  | RESISTOR, American symbol
R8 | 1 | R-US_R0805 | 22K | R0805 |  |  |  |  | RESISTOR, American symbol
R2 | 1 | R-US_R0805 | 39R | R0805 |  |  |  |  | RESISTOR, American symbol
R3 | 1 | R-US_R0805 | 39R | R0805 |  |  |  |  | RESISTOR, American symbol
R69 | 1 | R-US_R0805 | 60R4 | R0805 |  |  |  |  | RESISTOR, American symbol
R70 | 1 | R-US_R0805 | 60R4 | R0805 |  |  |  |  | RESISTOR, American symbol
R71 | 1 | R-US_R0805 | 60R4 | R0805 |  |  |  |  | RESISTOR, American symbol
R72 | 1 | R-US_R0805 | 60R4 | R0805 |  |  |  |  | RESISTOR, American symbol
R1 | 1 | R-US_R0805 | 100k | R0805 |  |  |  |  | RESISTOR, American symbol
R10 | 1 | R-US_R0805 | 330R | R0805 |  |  |  |  | RESISTOR, American symbol
R5 | 1 | R-US_R0805 | 402R | R0805 |  |  |  |  | RESISTOR, American symbol
R13 | 1 | R-US_R0805 | 402R | R0805 |  |  |  |  | RESISTOR, American symbol
R11 | 1 | R-US_R0805 | 680R | R0805 |  |  |  |  | RESISTOR, American symbol
Y2 | 1 | RESONATOR_EPSON_FC_145 | 32.768Khz | RESONATOR_EPSON_FC_145
J2 | 1 | S8421-45R |  | S8421-45R_1 | HARWIN | S8421-45R | 9094486 |  | Coin Cell Battery Holders EZ BDWR, SMT COIN CELL HOLDER CR2032
IC3 | 1 | SN65HVD234 | SN65HVD234 | SOIC8
IC4 | 1 | SN65HVD234 | SN65HVD234 | SOIC8
IC2 | 1 | SN74AHCT125D |  | SOIC127P600X175-14N | Texas Instruments | SN74AHCT125D | 526606 |  | Quad Bus Buffer w 3-State SN74AHCT125D
SJ1 | 1 | SOLDERJUMPERNC |  | SJ_2S |  |  |  |  | Solder JumperStandard SMD solder jumper. Used to automate production. Two varients : Normally Open and Normally Closed are the same, but have different paste layers. NC will have a large amount of paste and should jumper during reflow.
SJ2 | 1 | SOLDERJUMPERNC |  | SJ_2S |  |  |  |  | Solder JumperStandard SMD solder jumper. Used to automate production. Two varients : Normally Open and Normally Closed are the same, but have different paste layers. NC will have a large amount of paste and should jumper during reflow.
SJ3 | 1 | SOLDERJUMPERNC |  | SJ_2S |  |  |  |  | Solder JumperStandard SMD solder jumper. Used to automate production. Two varients : Normally Open and Normally Closed are the same, but have different paste layers. NC will have a large amount of paste and should jumper during reflow.
IC5 | 1 | ULN2003ADR |  | SOIC127P600X175-16N | Texas Instruments | ULN2003ADR | 6658699P |  | Trans Darlington NPN 50V 0.5A SOIC16 Texas Instruments ULN2003ADR, 7-element NPN Darlington Transistor Array, 0.5 A 50 V, 16-Pin SOIC
Z1 | 1 | VARISTORCN0603 | CG0603MLC-05E | CT/CN0603 |  |  |  |  | VARISTOR
Z2 | 1 | VARISTORCN0603 | CG0603MLC-05E | CT/CN0603 |  |  |  |  | VARISTOR
L2 | 1 | WE-CBF_0805 | MH2029-300Y | 805 |  |  |  |  | SMD EMI Suppression Ferrite Beads- excellent anti-EMI properties - low DCR- impedances till 3000 ohms- rated current up to 6 A
L3 | 1 | WE-CBF_0805 | MH2029-300Y | 805 |  |  |  |  | SMD EMI Suppression Ferrite Beads- excellent anti-EMI properties - low DCR- impedances till 3000 ohms- rated current up to 6 A
L4 | 1 | WE-CBF_0805 | MH2029-300Y | 805 |  |  |  |  | SMD EMI Suppression Ferrite Beads- excellent anti-EMI properties - low DCR- impedances till 3000 ohms- rated current up to 6 A
L5 | 1 | WE-CBF_0805 | MH2029-300Y | 805 |  |  |  |  | SMD EMI Suppression Ferrite Beads- excellent anti-EMI properties - low DCR- impedances till 3000 ohms- rated current up to 6 A

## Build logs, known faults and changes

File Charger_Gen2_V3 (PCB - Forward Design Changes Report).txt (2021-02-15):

Forward Design Changes Report
-----------------------------

Report Written:     Tuesday, December 18, 2018
Design Path:        C:\Users\tomde\Documents\GitHub\Tesla-Charger\Charger_Gen2_V3.pcb
Design Title:       
Created:            03-Oct-17 12:16:38 PM
Last Saved:         18-Dec-18 12:25:53 PM
Editing Time:       2190 min
Units:              mm (precision 2)

Disconnected pin "J2.2" from net "N0169".

Deleted net "N0169".

Connected pin "J2.2" to net "GND".

End Of Report.

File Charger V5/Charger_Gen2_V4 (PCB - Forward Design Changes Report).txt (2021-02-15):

Forward Design Changes Report
-----------------------------

Report Written:     Monday, January 21, 2019
Design Path:        C:\Users\tomde\Documents\GitHub\Tesla-Charger\Charger V5\Charger_Gen2_V4.pcb
Design Title:       
Created:            03-Oct-17 12:16:38 PM
Last Saved:         21-Jan-19 5:06:33 PM
Editing Time:       2537 min
Units:              mm (precision 2)

Disconnected pin "J1.1" from net "N0159".
Disconnected pin "J1.5" from net "N0162".

Deleted net "N0159".
Deleted net "N0162".

Connected pin "J1.1" to net "+5Vcc".
Connected pin "J1.5" to net "GND".

End Of Report.

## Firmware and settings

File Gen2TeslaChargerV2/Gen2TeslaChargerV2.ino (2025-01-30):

/*
  Tesla Gen 2 Charger Control Program
  2017-2018
  T de Bree
  D.Maguire
  Additional work by C. Kidder
  Runs on OpenSource Logic board V2 in Gen2 charger. Commands all modules.
*/

#include <can_common.h>
#include <due_can.h>
#include <due_wire.h>
#include <Wire_EEPROM.h>
#include <DueTimer.h>
#include "config.h"
#include <rtc_clock.h>  ///https://github.com/MarkusLange/Arduino-Due-RTC-Library
#include <PID_v1.h>

#define Serial SerialUSB

#define SUPC_KEY (0xA5)

template<class T> inline Print &operator<<(Print &obj, T arg) {
  obj.print(arg);
  return obj;
}

int firmware = 230822;

//////////////Set the hardware version/////////////////

//int hardware = BoardV5;
int hardware = BoardV4;

RTC_clock rtc_clock(XTAL);

int watchdogTime = 8000;

char *daynames[] = { "Mon", "Tue", "Wed", "Thu", "Fri", "Sat", "Sun" };

//////////////Setup PID for DC current regulation/////////////////

#define PIN_INPUT 0
#define PIN_OUTPUT 3

//Define Variables we'll be connecting to
double Setpoint, Input, Output;

//Specify the links and initial tuning parameters
double Kp = 2, Ki = 5, Kd = 1;
PID myPID(&Input, &Output, &Setpoint, Kp, Ki, Kd, DIRECT);


//*********GENERAL VARIABLE   DATA ******************
int evsedebug = 1;  // 1 = show Proximity status and Pilot current limmits
int debug = 1;      // 1 = show phase module CAN feedback


uint16_t curset = 0;
int setting = 1;
int incomingByte = 0;
int state;
unsigned long sleeptime, slavetimeout, tlast, tcan, tboot, droptime = 0;
bool dropsignal = 0;
bool bChargerEnabled;

float DCLim = 0;
int L1 = 0;

//**************Sleep Variables****************

//*********EVSE VARIABLE   DATA ******************
byte Proximity = 0;
uint16_t ACvoltIN = 240;  // AC input voltage 240VAC for EU/UK and 110VAC for US
//proximity status values for type 1
#define Unconnected 0  // 3.3V
#define Buttonpress 1  // 2.3V
#define Connected 2    // 1.35V

volatile uint32_t pilottimer = 0;
volatile uint16_t timehigh, duration = 0;
volatile uint16_t accurlim = 0;
volatile int dutycycle = 0;

uint16_t cablelim = 0;  // Type 2 cable current limit

//*********Single or Three Phase Config VARIABLE   DATA ******************

//proximity status values
#define Singlephase 0  // all parrallel on one phase Type 1
#define Threephase 1   // one module per phase Type 2

//*********Charger Control VARIABLE   DATA ******************
bool Vlimmode = true;  // Set charges to voltage limit mode
uint16_t modulelimcur, dcaclim = 0;
uint32_t maxaccur = 16000;  //maximum AC current in mA
uint16_t maxdccur = 45000;  //max DC current outputin mA
int activemodules, slavechargerenable = 0;
bool LockOut = false;     //lockout on termination voltage reached. Reset by evse plug recycle.
uint16_t LockOutCnt = 0;  // lockout counter


//*********Feedback from charge VARIABLE   DATA ******************
uint16_t dcvolt[3] = { 0, 0, 0 };  //1 = 1V
uint16_t dccur[3] = { 0, 0, 0 };
uint16_t totdccur = 0;             //1 = 0.005Amp
uint16_t acvolt[3] = { 0, 0, 0 };  //1 = 1V
uint16_t accur[3] = { 0, 0, 0 };   //1 = 0.06666 Amp
long acpower = 0;
byte inlettarg[3] = { 0, 0, 0 };                    //inlet target temperatures, should be used to command cooling.
byte curtemplim[3] = { 0, 0, 0 };                   //current limit due to temperature
byte templeg[2][3] = { { 0, 0, 0 }, { 0, 0, 0 } };  //temperatures reported back
bool ACpres[3] = { 0, 0, 0 };                       //AC present detection on the modules
bool ModEn[3] = { 0, 0, 0 };                        //Module enable feedback on the modules
bool ModFlt[3] = { 0, 0, 0 };                       //module fault feedback
byte ModStat[3] = { 0, 0, 0 };                      //Module Status
int newframe = 0;

ChargerParams parameters;

//*********DCDC Messages VARIABLE   DATA ******************
bool dcdcenable = 0;  // turn on can messages for the DCDC.

//*********Charger Messages VARIABLE   DATA ******************
int ControlID = 0x300;
int StatusID = 0x410;
unsigned long ElconID = 0x18FF50E5;
unsigned long ElconControlID = 0x1806E5F4;


int candebug = 0;
int menuload = 0;

// this function has to be present, otherwise watchdog won't work
void watchdogSetup(void) {
  // do what you want here
}

void setup() {
  pmc_set_writeprotect(false);
  pmc_mck_set_prescaler(16);

  // 12MHz / 64 * 14 = 2.625MHz //  96 = 110 << 4 = /64
  // 12MHz / 32 * 14 = 5.25 MHz //  80 = 101 << 4 = /32
  // 12MHz / 16 * 14 = 10.5 MHz //  64 = 100 << 4 = /16
  // 12MHz /  8 * 14 = 21   MHz //  48 = 011 << 4 = /8
  // 12MHz /  4 * 14 = 42   MHz //  32 = 010 << 4 = /4
  // 12MHz /  2 * 14 = 84   MHz //  16 = 001 << 4 = /2 (default)

  pmc_disable_periph_clk(22);  // TWI/I2C bus 0 (i.MX6 controlling)
  pmc_disable_periph_clk(23);  // TWI/I2C bus 1
  pmc_disable_periph_clk(24);  // SPI0
  pmc_disable_periph_clk(25);  // SPI1
  pmc_disable_periph_clk(26);  // SSC (I2S digital audio, N/C)

  pmc_disable_periph_clk(41);  // random number generator
  pmc_disable_periph_clk(42);  // ethernet MAC - N/C


  Serial.begin(115200);  //Initialize our USB port which will always be redefined as SerialUSB to use the Native USB port tied directly to the SAM3X processor.

  Timer3.attachInterrupt(Ext_msgs).start(90000);  // charger messages every 100ms

  attachInterrupt(EVSE_PILOT, Pilotread, CHANGE);
  watchdogEnable(watchdogTime);
  Wire.begin();
  EEPROM.read(0, parameters);
  if (parameters.version != EEPROM_VERSION) {
    parameters.version = EEPROM_VERSION;
    parameters.currReq = 0;            //max input limit per module 1500 = 1A
    parameters.enabledChargers = 123;  // enable per phase - 123 is all phases - 3 is just phase 3
    parameters.can0Speed = 500000;
    parameters.can1Speed = 250000;
    parameters.mainsRelay = 48;
    parameters.voltSet = 32000;           //1 = 0.01V
    parameters.tVolt = 34000;             //1 = 0.01V
    parameters.autoEnableCharger = 0;     //disable auto start, proximity and pilot control
    parameters.canControl = 0;            //0 disabled can control, 1 master, 3 slave
    parameters.dcdcsetpoint = 14000;      //voltage setpoint for dcdc in mv
    parameters.phaseconfig = Threephase;  //AC input configuration
    parameters.type = 2;                  //Socket type1 or 2
    parameters.sleeptimeout = 30000;      // mS before entering sleep
    EEPROM.write(0, parameters);
  }

  ////rtc clock start///////

  rtc_clock.init();

  //rtc_clock.set_time(19, 35, 0);
  //rtc_clock.set_date(16, 11, 2018);

  // Initialize CAN ports
  if (Can1.begin(parameters.can1Speed, 255))  //can1 external bus
  {
    Serial.println("Using CAN1 - initialization completed.\n");
  } else Serial.println("CAN1 initialization (sync) ERROR\n");


  // Initialize CAN0
  if (Can0.begin(parameters.can0Speed, 255))  //can0 charger modules
  {
    Serial.println("Using CAN0 - initialization completed.\n");
  } else Serial.println("CAN0 initialization (sync) ERROR\n");

  int filter;
  //extended
  for (filter = 0; filter < 3; filter++) {
    Can0.setRXFilter(filter, 0, 0, true);
    Can1.setRXFilter(filter, 0, 0, true);
  }
  //standard
  for (int filter = 3; filter < 7; filter++) {
    Can0.setRXFilter(filter, 0, 0, false);
    Can1.setRXFilter(filter, 0, 0, false);
  }
  ///////////////////CHARGER ENABLE AND ACTIVATE LINES///////////////////////////////////

  //////////////////////////////////////////////////////////////////////////////////////

  ///////////////////CHARGER ENABLE AND ACTIVATE LINES///////////////////////////////////
  pinMode(LED_BUILTIN, OUTPUT);
  pinMode(CHARGER1_ENABLE, OUTPUT);    //CHG1 ENABLE
  pinMode(CHARGER2_ENABLE, OUTPUT);    //CHG2 ENABLE
  pinMode(CHARGER3_ENABLE, OUTPUT);    //CHG3 ENABLE
  pinMode(CHARGER1_ACTIVATE, OUTPUT);  //CHG1 ACTIVATE
  pinMode(CHARGER2_ACTIVATE, OUTPUT);  //CHG2 ACTIVATE
  pinMode(CHARGER3_ACTIVATE, OUTPUT);  //CHG3 ACTIVATE

  digitalWrite(CHARGER1_ACTIVATE, LOW);  //chargeph1 deactivate
  digitalWrite(CHARGER2_ACTIVATE, LOW);  //chargeph2 deactivate
  digitalWrite(CHARGER3_ACTIVATE, LOW);  //chargeph3 deactivate
  digitalWrite(CHARGER1_ENABLE, LOW);    //disable phase 1 power module
  digitalWrite(CHARGER2_ENABLE, LOW);    //disable phase 2 power module
  digitalWrite(CHARGER3_ENABLE, LOW);    //disable phase 3 power module
  //////////////////////////////////////////////////////////////////////////////////////


  pinMode(DIG_IN_1, INPUT);  //IP1
  pinMode(DIG_IN_2, INPUT);  //IP2
  //////////////////////////////////////////////////////////////////////////////////////

  //////////////DIGITAL OUTPUTS MAPPED TO X046. 10 PIN CONNECTOR ON LEFT//////////////////////////////////////////
  pinMode(DIG_OUT_1, OUTPUT);      //OP1 - X046 PIN 6
  pinMode(DIG_OUT_2, OUTPUT);      //OP2
  pinMode(DIG_OUT_3, OUTPUT);      //OP2
  pinMode(DIG_OUT_4, OUTPUT);      //OP3
  pinMode(EVSE_ACTIVATE, OUTPUT);  //pull Pilot to 6V

  digitalWrite(EVSE_ACTIVATE, LOW);
  digitalWrite(DIG_OUT_1, LOW);  //MAINS OFF
  digitalWrite(DIG_OUT_2, LOW);  //AC OFF when in manual mode.
  digitalWrite(DIG_OUT_3, LOW);
  digitalWrite(DIG_OUT_4, LOW);
  ///////////////////////////////////////////////////////////////////////////////////////

  ///////////////Setup Sleep Mode Wake Ups////////////////////////////////////////////////////////////////////////

  uint16_t tmp = ((1 << 12) | (1 << 5) | (1 << 1) | 1);  // Wake up on CAN1 RX AND D19 AND D60 AND CAN0 RX
  SUPC->SUPC_WUIR = tmp;                                 // above sources, low-> high transition
  SUPC->SUPC_WUMR = 0;                                   // try no debouncing; 1 << 12 for 3 cycle

  ///////////////////////////////////////////////////////////////////////////////////////
  dcaclim = maxaccur;
  bChargerEnabled = false;  //are we supposed to command the charger to charge?
  //

  myPID.SetMode(AUTOMATIC);  //start PID

  sleeptime = millis();  //update timer
}

void loop() {
  CAN_FRAME incoming;

  if (Can0.available()) {
    Can0.read(incoming);
    candecode(incoming);
    sleeptime = millis();  //update timer
  }

  if (Can1.available()) {
    //Serial.println();
    //Serial.print("can 1 data");
    Can1.read(incoming);
    canextdecode(incoming);
    sleeptime = millis();  //update timer
  }

  if (Serial.available()) {
    menu();
    sleeptime = millis();  //update timer
  }

  if (parameters.canControl > 1) {
    if (state != 0) {
      if (millis() - tcan > 2000) {
        state = 0;
        Serial.println();
        Serial.println("CAN time-out");
      }
    }
  }

  if (digitalRead(DIG_IN_1) == LOW) {
    state = 0;
  }

  switch (state) {
    case 0:  //Charger off
      //Serial.println();
      //Serial.println("Enter State 0");
      //Serial.println();
      if (bChargerEnabled == true) {
        bChargerEnabled = false;
      }
      digitalWrite(DIG_OUT_1, LOW);  //MAINS OFF\
      digitalWrite(EVSE_ACTIVATE, LOW);
      //digitalWrite(DIG_OUT_2, LOW);//AC OFF when in manual mode.
      digitalWrite(CHARGER1_ACTIVATE, LOW);  //chargeph1 deactivate
      digitalWrite(CHARGER2_ACTIVATE, LOW);  //chargeph2 deactivate
      digitalWrite(CHARGER3_ACTIVATE, LOW);  //chargeph3 deactivate
      digitalWrite(CHARGER1_ENABLE, LOW);    //disable phase 1 power module
      digitalWrite(CHARGER2_ENABLE, LOW);    //disable phase 2 power module
      digitalWrite(CHARGER3_ENABLE, LOW);    //disable phase 3 power module
      for (int y; y < 3; y++) {
        dcvolt[y] = 0;
        dccur[y] = 0;
        totdccur = 0;  //1 = 0.005Amp
        acvolt[y] = 0;
        accur[y] = 0;
      }
      break;

    case 1:                  //Charger on
      sleeptime = millis();  //update timer
      if (digitalRead(DIG_IN_1) == HIGH) {
        if (bChargerEnabled == false) {
          bChargerEnabled = true;
          switch (parameters.enabledChargers) {
            case 1:
              digitalWrite(CHARGER1_ACTIVATE, HIGH);
              activemodules = 1;
              break;
            case 2:
              digitalWrite(CHARGER2_ACTIVATE, HIGH);
              activemodules = 1;
              break;
            case 3:
              digitalWrite(CHARGER3_ACTIVATE, HIGH);
              activemodules = 1;
              break;
            case 12:
              digitalWrite(CHARGER1_ACTIVATE, HIGH);
              digitalWrite(CHARGER2_ACTIVATE, HIGH);
              activemodules = 2;
              break;
            case 13:
              digitalWrite(CHARGER1_ACTIVATE, HIGH);
              digitalWrite(CHARGER3_ACTIVATE, HIGH);
              activemodules = 2;
              break;
            case 123:
              digitalWrite(CHARGER1_ACTIVATE, HIGH);
              digitalWrite(CHARGER2_ACTIVATE, HIGH);
              digitalWrite(CHARGER3_ACTIVATE, HIGH);
              activemodules = 3;
              break;
            case 23:
              digitalWrite(CHARGER2_ACTIVATE, HIGH);
              digitalWrite(CHARGER3_ACTIVATE, HIGH);
              activemodules = 2;
              break;
            default:
              // if nothing else matches, do the default
              // default is optional
              break;
          }
          delay(100);
          digitalWrite(DIG_OUT_1, HIGH);  //MAINS ON
          digitalWrite(EVSE_ACTIVATE, HIGH);
          digitalWrite(DIG_OUT_2, HIGH);  //AC on in manual mode
        }
      } else {
        bChargerEnabled = false;
        state = 0;
      }
      break;

    case 2:
      switch (parameters.enabledChargers) {
        case 1:
          digitalWrite(CHARGER1_ENABLE, HIGH);  //enable phase 1 power module
          break;
        case 2:
          digitalWrite(CHARGER2_ENABLE, HIGH);  //enable phase 2 power module
          break;
        case 3:
          digitalWrite(CHARGER3_ENABLE, HIGH);  //enable phase 3 power module
          break;
        case 12:
          digitalWrite(CHARGER1_ENABLE, HIGH);  //enable phase 1 power module
          digitalWrite(CHARGER2_ENABLE, HIGH);  //enable phase 2 power module
          break;
        case 13:
          digitalWrite(CHARGER1_ENABLE, HIGH);  //enable phase 1 power module
          digitalWrite(CHARGER3_ENABLE, HIGH);  //enable phase 3 power module
          break;
        case 123:
          digitalWrite(CHARGER1_ENABLE, HIGH);  //enable phase 1 power module
          digitalWrite(CHARGER2_ENABLE, HIGH);  //enable phase 2 power module
          digitalWrite(CHARGER3_ENABLE, HIGH);  //enable phase 3 power module
          break;
        case 23:
          digitalWrite(CHARGER2_ENABLE, HIGH);  //enable phase 2 power module
          digitalWrite(CHARGER3_ENABLE, HIGH);  //enable phase 3 power module
          break;

        default:
          // if nothing else matches, do the default
          break;
      }
      if (tboot < (millis() - 1000))  //delay in ms before moving to state 1.
      {
        state = 1;
      }

    default:
      // if nothing else matches, do the default
      break;
  }
  if (tlast < (millis() - 500)) {
    tlast = millis();
    evseread();
    //autoShutdown();
    watchdogReset();
    if (debug != 0) {
      if (hardware == BoardV5) {
        if (millis() - sleeptime > parameters.sleeptimeout - 10000) {
          Serial.println();
          Serial.println();
          Serial.println();
          Serial.print("!!!!! Sleep in: ");
          Serial.print((sleeptime - (millis() - parameters.sleeptimeout)) * 0.001);
          Serial.print(" S");
        }
      }
      Serial.println();
      Serial.print(millis());
      Serial.print(" State: ");
      Serial.print(state);
      Serial.print(" Phases : ");
      Serial.print(parameters.phaseconfig);
      Serial.print(" Modules Active : ");
      Serial.print(activemodules);
      if (bChargerEnabled) {
        Serial.print(" ON  ");
      } else {
        Serial.print(" OFF ");
      }
      if (digitalRead(DIG_IN_1) == HIGH) {
        Serial.print(" D1 H");
      } else {
        Serial.print(" D1 L");
      }
      if (digitalRead(DIG_OUT_1) == HIGH) {
        Serial.print(" O1 H");
      } else {
        Serial.print(" O1 L");
      }
      if (digitalRead(DIG_OUT_2) == HIGH) {
        Serial.print(" O2 H");
      } else {
        Serial.print(" O2 L");
      }
      Serial.print(" Droptime : ");
      Serial.print(droptime);
      if (bChargerEnabled) {
        Serial.println();
        for (int x = 0; x < 3; x++) {
          Serial.print("  Phase ");
          Serial.print(x + 1);
          Serial.print(" Feebback //  AC present: ");
          Serial.print(ACpres[x]);
          Serial.print("  AC volt: ");
          Serial.print(acvolt[x]);
          Serial.print("  AC cur: ");
          Serial.print((accur[x] * 0.06666), 2);
          //Serial.print("  ");
          ///Serial.print(accur[x], HEX); ///not needed since current fixed
          Serial.print("  DC volt: ");
          Serial.print(dcvolt[x]);
          Serial.print("  DC cur: ");
          Serial.print(dccur[x], 2);
          Serial.print("  Inlet Targ: ");
          Serial.print(inlettarg[x]);
          Serial.print("  Temp Lim Cur: ");
          Serial.print(curtemplim[x]);
          Serial.print("  ");
          Serial.print(templeg[0][x]);
          Serial.print("  ");
          Serial.print(templeg[1][x]);
          Serial.print(" EN:");
          Serial.print(ModEn[x]);
          Serial.print(" Flt:");
          Serial.print(ModFlt[x]);
          Serial.print(" Stat:");
          Serial.print(ModStat[x], BIN);
          Serial.println();
        }
      } else {
        Serial.println();
        Serial.print("Modules Turned OFF");
        Serial.println();
      }
    }
    if (debug == 1) {
      if (evsedebug != 0) {
        Serial.println();
        Serial.print("  Proximity Status : ");
        switch (Proximity) {
          case Unconnected:
            Serial.print("Unconnected");
            break;
          case Buttonpress:
            Serial.print("Button Pressed");
            break;
          case Connected:
            Serial.print("Connected");
            break;
        }
        Serial.print(" AC limit : ");
        Serial.print(accurlim);
        Serial.print(" /Cable Limit: ");
        Serial.print(cablelim);
        Serial.print(" /Module Cur Request: ");
        Serial.print(modulelimcur / 1.5, 0);
        Serial.print(" /DC total Cur:");
        Serial.print(totdccur, 2);
        Serial.print(" /DC Setpoint:");
        Serial.print(parameters.voltSet * 0.01, 0);
        Serial.print(" /DC Lim: ");
        Serial.print(maxdccur);
      }
    }
  }
  //DCcurrentlimit();
  DClimCalc();
  ACcurrentlimit();

  //resetFaults();

  //EVSE automatic control

  if (parameters.autoEnableCharger == 1) {
    if (Proximity == Connected)  //check if plugged in
    {
      //digitalWrite(EVSE_ACTIVATE, HIGH);//pull pilot low to indicate ready - NOT WORKING freezes PWM reading
      if (accurlim > 1400)  // one amp or more active modules
      {
        if (state == 0) {
          if (digitalRead(DIG_IN_1) == HIGH) {
            state = 2;  // initialize modules
            tboot = millis();
          }
        }
      }
      digitalWrite(DIG_OUT_2, HIGH);  //enable AC present indication
    } else                            // unplugged or buton pressed stop charging
    {
      if (dropsignal == 0) {
        droptime == millis();
        dropsignal == 1;
      } else {
        if (millis() - millis() < 1000) {
          state = 0;
          digitalWrite(DIG_OUT_2, LOW);  //disable AC present indication
          dropsignal == 0;
        }
      }
    }
  }
  if (hardware == BoardV5)  ///Ensure to only sleep on boards that can wake up
  {
    if (millis() - sleeptime > parameters.sleeptimeout && menuload != 1) {
      Serial.println();
      Serial.println();
      Serial.print("Entering Sleep");
      delay(10);
      pmc_enable_backupmode();
    }
  }


}  //end of loop

///////////////////////////////////////////////////////////////////////////////////////////////////////////////////////////////////////////////////////
//If a charger power module is running and faults out we want to reset and go again otherwise charger can just sit there and not finish a charge.
///////////////////////////////////////////////////////////////////////////////////////////////////////////////////////////////////////////////////////
void resetFaults() {


  if ((bChargerEnabled == true) && (ACpres[0] == true) && (ModFlt[0] == true) && ((parameters.enabledChargers == 1) || (parameters.enabledChargers == 12) || (parameters.enabledChargers == 13) || (parameters.enabledChargers == 123))) {
    //if these conditions are met then phase one is enabled, has ac present and has entered a fault state so we want to reset.
    state = 0;
    //digitalWrite(DIG_OUT_2, LOW); //disable AC present indication;
    //  digitalWrite(EVSE_ACTIVATE, LOW);
  }
  if ((bChargerEnabled == true) && (ACpres[1] == true) && (ModFlt[1] == true) && ((parameters.enabledChargers == 2) || (parameters.enabledChargers == 12) || (parameters.enabledChargers == 23) || (parameters.enabledChargers == 123))) {
    //if these conditions are met then phase two is enabled, has ac present and has entered a fault state so we want to reset.
    state = 0;
    //digitalWrite(DIG_OUT_2, LOW); //disable AC present indication;
    //digitalWrite(EVSE_ACTIVATE, LOW);
  }
  if ((bChargerEnabled == true) && (ACpres[2] == true) && (ModFlt[2] == true) && ((parameters.enabledChargers == 3) || (parameters.enabledChargers == 13) || (parameters.enabledChargers == 23) || (parameters.enabledChargers == 123))) {
    //if these conditions are met then phase three is enabled, has ac present and has entered a fault state so we want to reset.
    state = 0;
    //digitalWrite(DIG_OUT_2, LOW); //disable AC present indication;
    //digitalWrite(EVSE_ACTIVATE, LOW);
  }
}

///////////////////////////////////////////////////////////////////////////////////////////////////////////////////////////////////////////////////////
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

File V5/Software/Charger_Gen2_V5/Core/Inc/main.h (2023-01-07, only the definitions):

#define LED_PIN_Pin GPIO_PIN_13
#define LED_PIN_GPIO_Port GPIOC
#define DIG_OUT_1_Pin GPIO_PIN_2
#define DIG_OUT_1_GPIO_Port GPIOA
#define DIG_OUT_2_Pin GPIO_PIN_3
#define DIG_OUT_2_GPIO_Port GPIOA
#define DIG_OUT_3_Pin GPIO_PIN_4
#define DIG_OUT_3_GPIO_Port GPIOA
#define EVSE_PILOT_Pin GPIO_PIN_6
#define EVSE_PILOT_GPIO_Port GPIOA
#define EVSE_PILOT_EXTI_IRQn EXTI9_5_IRQn
#define CHARGER3_ENABLE_Pin GPIO_PIN_12
#define CHARGER3_ENABLE_GPIO_Port GPIOB
#define CHARGER2_ENABLE_Pin GPIO_PIN_13
#define CHARGER2_ENABLE_GPIO_Port GPIOB
#define CHARGER1_ENABLE_Pin GPIO_PIN_14
#define CHARGER1_ENABLE_GPIO_Port GPIOB
#define EVSE_ACTIVATE_Pin GPIO_PIN_15
#define EVSE_ACTIVATE_GPIO_Port GPIOB
#define DIG_IN_1_Pin GPIO_PIN_3
#define DIG_IN_1_GPIO_Port GPIOB
#define DIG_IN_2_Pin GPIO_PIN_4
#define DIG_IN_2_GPIO_Port GPIOB
#define CHARGER1_ACTIVATE_Pin GPIO_PIN_5
#define CHARGER1_ACTIVATE_GPIO_Port GPIOB
#define CHARGER2_ACTIVATE_Pin GPIO_PIN_6
#define CHARGER2_ACTIVATE_GPIO_Port GPIOB
#define CHARGER3_ACTIVATE_Pin GPIO_PIN_7
#define CHARGER3_ACTIVATE_GPIO_Port GPIOB

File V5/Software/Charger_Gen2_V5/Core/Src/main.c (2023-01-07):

/**
  ******************************************************************************
  * @file           : main.c
  * @brief          : Main program body
  *
  *
  *   Tesla Gen 2 Charger Control Program
  *	2017-2019
  *T de Bree
  *D.Maguire
  *Additional work by C. Kidder
  *Runs on OpenSource Logic board V5 in Gen2 charger. Commands all modules.

 	 *D.Maguire 2019 Mods :
*	-Stop sending power module can messages when charger not running - Working.
*	-Correct reading of charger Fault and Enable feedback signals - Working.
*	-Correct AC present flag so only sets if more than 70V AC is on each module - Working.
*	-Reset charger on detection of power module fault - Testing.
*	-Shutdown on exceeding a preset HV Battery voltage - Working.
*	-Evse read routine now in 500ms loop to prevent false triggering -Working.
*	-Added counter/timer to autoshutdown to prevent false triggering on transients -Working.
*	-Added manual control mode for use of charger without EVSE. Digital one in when brought to +12v commands the charger to start
*	and when brought low commands charger off. This mode also control HVDC via digital out 1 and AC mains via a contactor via Digital out 2.-Working.
  *
  * Ported to the STM32F103 based V5 board in 2020 by Köksal Kurt.
  *
  * Serial Console on USART1
  *
  * WiFi access via USART3 and ESP8266 module
  *
  ******************************************************************************
  *
  ******************************************************************************
  */

/* Includes ------------------------------------------------------------------*/
#include "main.h"
#include "adc.h"
#include "can.h"
#include "rtc.h"
#include "tim.h"
#include "usart.h"
#include "usb.h"
#include "gpio.h"
#include "config.h"
#include "stdbool.h"
#include "stdint.h"
#include "eeprom.h"
#include "string.h"
#include "stdio.h"
#include "stdlib.h"


/* Private typedef -----------------------------------------------------------*/
CAN_TxHeaderTypeDef myTxMessage; //CAN Tx message header

CAN_RxHeaderTypeDef myRxMessage; //CAN Rx message header

uint32_t              TxMailbox; //CAN Tx Mailbox ID


/* Private define ------------------------------------------------------------*/
#ifdef __GNUC__
  /* With GCC, small printf (option LD Linker->Libraries->Small printf
     set to 'Yes') calls __io_putchar() */
  #define PUTCHAR_PROTOTYPE int __io_putchar(int ch)
#else
  #define PUTCHAR_PROTOTYPE int fputc(int ch, FILE *f)
#endif /* __GNUC__ */

/* Private macro -------------------------------------------------------------*/


/* Private variables ---------------------------------------------------------*/

char wifistr[75];
uint8_t CanRxData[8];
uint8_t CanTxData[8];

int watchdogTime = 8000;

char* daynames[] = {"Mon", "Tue", "Wed", "Thu", "Fri", "Sat", "Sun"};


//*********GENERAL VARIABLE   DATA ******************
int evsedebug = 1; // 1 = show Proximity status and Pilot current limits
int debug = 1; // 1 = show phase module CAN feedback


uint16_t curset = 0;
int  setting = 1;
uint8_t incomingByte = 0;
int state;
unsigned long slavetimeout, tlast, tcan,tpause, tboot = 0;
bool bChargerEnabled;
uint8_t Uart_Rx[5];



//*********EVSE VARIABLE   DATA ******************
uint8_t Proximity = 0;
uint16_t ACvoltIN = 240; // AC input voltage 240VAC for EU/UK and 110VAC for US
//proximity status values for type 1
#define Unconnected 0 // 3.3V
#define Buttonpress 1 // 2.3V
#define Connected 2 // 1.35V

volatile uint32_t pilottimer = 0;
volatile uint16_t timehigh, duration = 0;
volatile uint16_t accurlim = 0;
volatile int dutycycle = 0;

uint16_t cablelim = 0; // Type 2 cable current limit
uint16_t val=0;
//*********Single or Three Phase Config VARIABLE   DATA ******************

//proximity status values
#define Singlephase 0 // all parrallel on one phase Type 1
#define Threephase 1 // one module per phase Type 2

//*********Charger Control VARIABLE   DATA ******************
bool Vlimmode = true; // Set charges to voltage limit mode
uint16_t modulelimcur, dcaclim = 0;
uint16_t maxaccur = 16000; //maximum AC current in mA
uint16_t maxdccur = 45000; //max DC current outputin mA
int activemodules, slavechargerenable = 0;



//*********Feedback from charge VARIABLE   DATA ******************
uint16_t dcvolt[3] = {0, 0, 0};//1 = 1V
uint16_t dccur[3] = {0, 0, 0};
uint16_t totdccur = 0;//1 = 0.005Amp
uint16_t acvolt[3] = {0, 0, 0};//1 = 1V
uint16_t accur[3] = {0, 0, 0};//1 = 0.06666 Amp
long acpower = 0;
uint8_t inlettarg [3] = {0, 0, 0}; //inlet target temperatures, should be used to command cooling.
uint8_t curtemplim [3] = {0, 0, 0};//current limit due to temperature
uint8_t templeg[2][3] = {{0, 0, 0}, {0, 0, 0}}; //temperatures reported back
bool ACpres [3] = {0, 0, 0}; //AC present detection on the modules
bool ModEn [3] = {0, 0, 0}; //Module enable feedback on the modules
bool ModFlt [3] = {0, 0, 0}; //module fault feedback
bool LockOut = false; //lockout on termination voltage reached. Reset by evse plug recycle.
uint8_t ModStat [3] = {0, 0, 0};//Module Status
int newframe = 0;

ChargerParams parameters;

//*********DCDC Messages VARIABLE   DATA ******************
bool dcdcenable = 1; // turn on can messages for the DCDC.

//*********Charger Messages VARIABLE   DATA ******************
int ControlID = 0x300;
int StatusID = 0x410;
unsigned long ElconID = 0x18FF50E5;
unsigned long ElconControlID = 0x1806E5F4;

uint16_t LockOutCnt=0;// lockout counter

int candebug = 0;
int menuload = 0;
int mescycle = 0;

uint16_t VirtAddVarTab[14]={20777,20778,20779,20780,20781,20782,20783,20784,20785,20786,20787,20788,20789,20790};

/* Private function prototypes -----------------------------------------------*/
void SystemClock_Config(void);
void EEPROM_Read(ChargerParams *tempparams);
void EEPROM_Write(ChargerParams *tempparams);
bool CAN_FilterConfig(void);
bool Can_Init(void);
void candecode(CAN_RxHeaderTypeDef *tempRx,uint8_t *tempCanData);
void menu(void);
uint32_t millis(void);
uint32_t micros(void);
void delay(uint32_t dly);
void Charger_msgs(void);
void resetFaults(void);
void evseread(void);
void autoShutdown(void);

void manualMode(void);
void DCcurrentlimit(void);
void ACcurrentlimit(void);
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

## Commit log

2017-10-21 Update Tesla_chg1_1.ino
    Made it serial controlled with change able voltage and current setpoints
    Will implement current ramp up now.
2017-10-21 Update and rename Tesla_chg1_1.ino to Tesla_chg1_2.ino
    Now with current ramp that is programmable
2017-10-21 Update Tesla_chg1_2.ino
    now with canbus decoding, unproven. Displaying can be toggled with debug.
2017-10-22 Update Tesla_chg1_2.ino
    updated to fix missing variable and correct spelling
    [Tesla_chg1_2.ino]
2017-10-24 Update Tesla_charger_Tom_v1.ino
    fixed current scaling, Damien please confirm this works.
    [Tesla_charger_Tom_v1.ino]
2021-02-15 Add Tesla Charger
    [BOM Charger_Gen2_V5190128.ods, Charger_Gen2_V3 (Bill Of Materials).csv, Charger_Gen2_V3 (Component Positions CSV).csv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]
2023-01-07 Added Average Filter

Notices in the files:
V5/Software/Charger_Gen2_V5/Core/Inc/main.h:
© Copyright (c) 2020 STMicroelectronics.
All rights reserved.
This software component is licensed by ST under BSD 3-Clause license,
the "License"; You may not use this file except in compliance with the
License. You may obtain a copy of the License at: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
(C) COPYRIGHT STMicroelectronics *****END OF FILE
